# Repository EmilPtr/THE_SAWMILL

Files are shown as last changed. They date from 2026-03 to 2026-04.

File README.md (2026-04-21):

# The Sawmill
The Sawmill is an antweight combat robot I made for the funzies to introduce myself to the wonderful world of combat robotics! This is... THE SAWMILL!!!!!!!!!!!

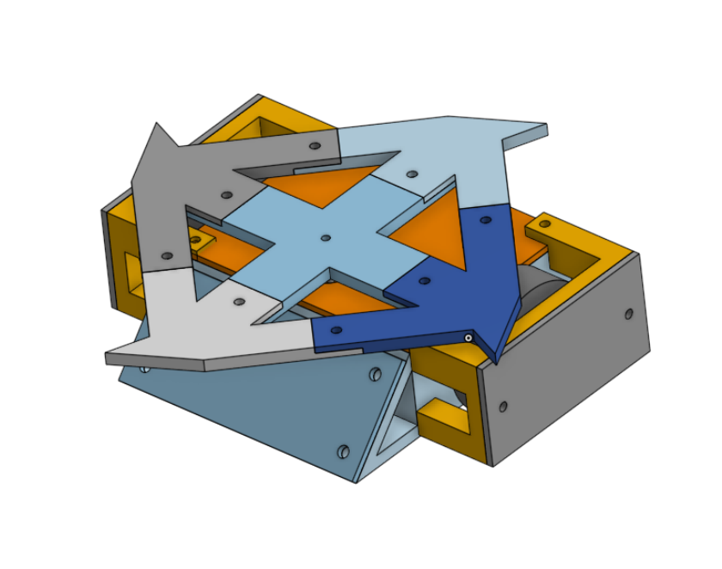
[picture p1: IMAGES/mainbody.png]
mainbody


Inspired by the Fingertech Viper with its horizontal spinner addon, the Sawmill is a wedge x horizontal spinner robot. If the blade decides to combust mid match, it's still a solid wedge bot!

(Disclaimer, this bot is not competetive, and would likely freaking explode in the box, it's made just for fun!)

It is primarily constructed from PLA, with M4 bolts and nuts for joining parts with heat set inserts, and aluminum plates to protect the vulnerable wheels and wedge.

## Design Planning
### Electronics
The electronics are basically your generic RC airplane stack combined with an Arduino Nano to control motors.

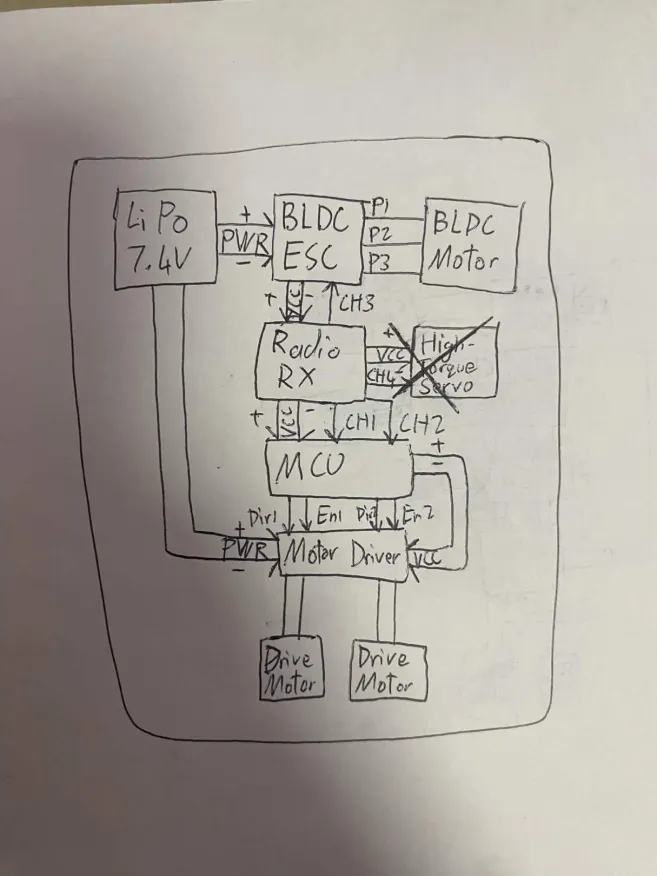
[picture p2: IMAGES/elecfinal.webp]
elec plan


The Arduino nano essentially "hijacks" the signals from the Radio RX, and parses these signals to power a TB6612FNG Motor Driver, the drive motors are N20s geared for 700RPM, while the weapon motor is an A2212 BLDC motor at 2200KV (I know it's a bit fast for a weapon, but :P I no wann spend monny)

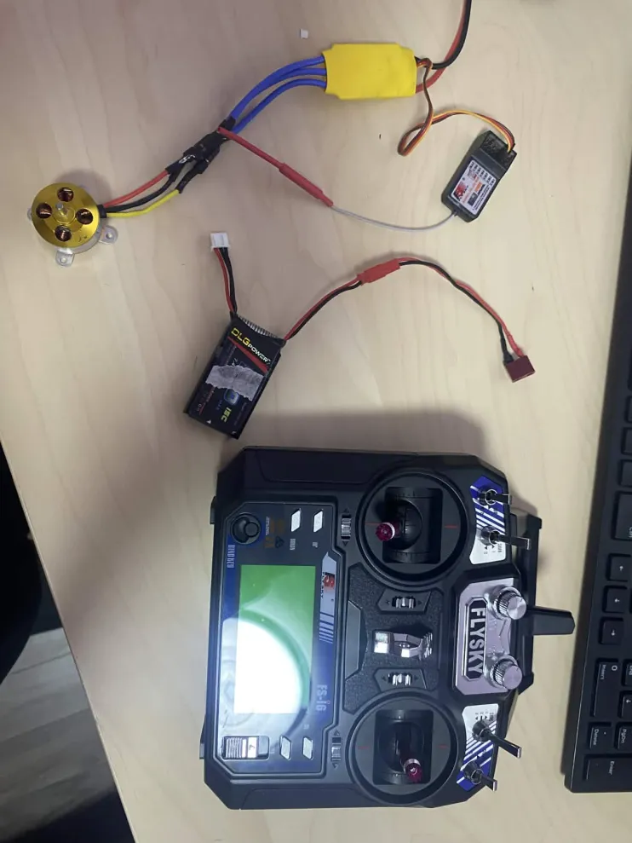
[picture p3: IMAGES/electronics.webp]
physical


Electronics excluding Arduino Nano and N20s, basically your generic RC airplane stack.

### Robot Concept
I am a very indecisive person! It is a very common occurence in my life where the and second/third attempt at something is always the best, while the first is genuinely terrible... I first went for a vertical spinner.

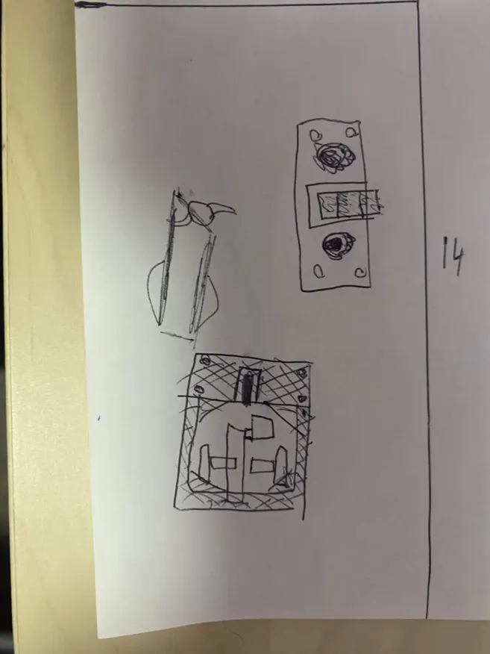
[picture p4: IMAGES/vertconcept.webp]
vert spinner


The vertical spinner concept

After realizing the manufacturing complexity and how accurate my build has to be so the spinner doesnt vibrate itself to death, I decided to switch to a horizontal spinner like Tombstone.

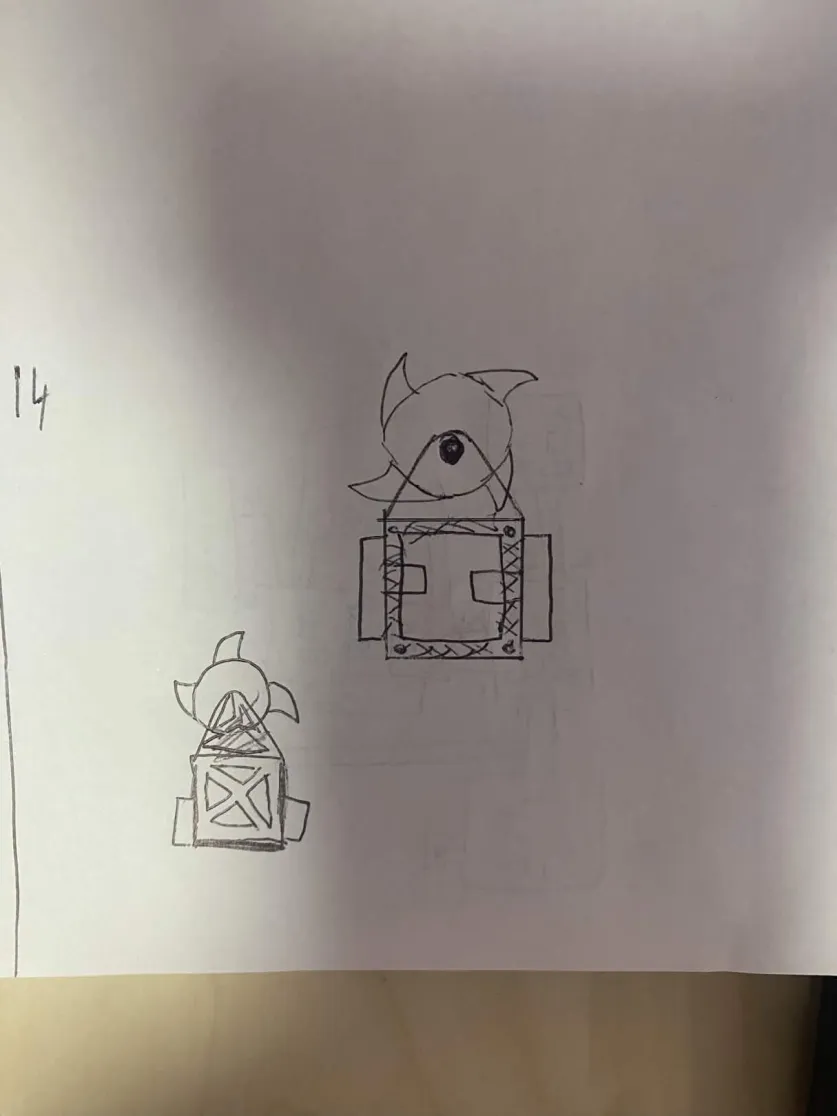
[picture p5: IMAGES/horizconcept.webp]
horizontal spinner


The horizontal spinner concept

I tried this and even got 3 hours of CAD in, I realized it would also be hard to implement, and horizontal spinners like tombstone have the highest self-KO rate, and are NOT beginner friendly

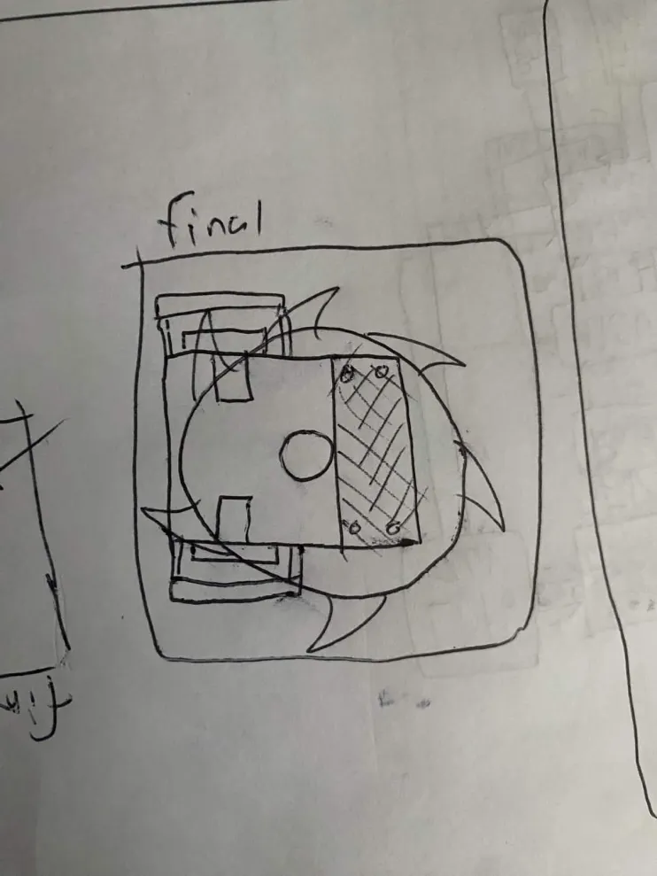
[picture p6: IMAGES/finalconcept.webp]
final


Final concept.

I decided to go with my final design after a few hours of dilly-dallying, and I'm pretty happy with it

## CAD
After I dealt with that kerfuffle... I started the CAD!!! I used OnShape because OnShape is so amazingly BASED and easy to use and FREE! I'm also really familiar with OnShape, but I learned so much from this, especially in Assembly and Drawings!

mainbody

Main body

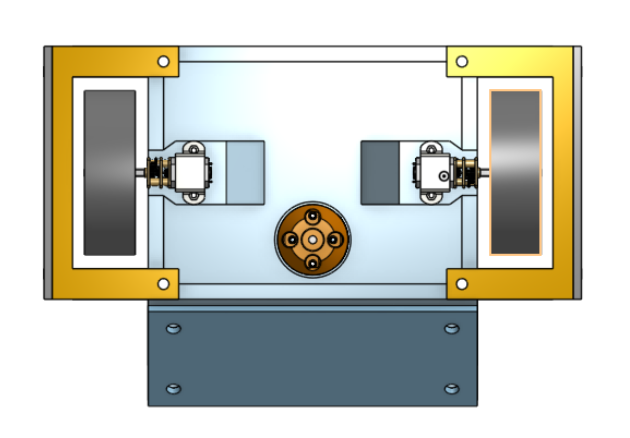
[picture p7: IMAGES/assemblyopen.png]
mainbodyopen


Main body open hood

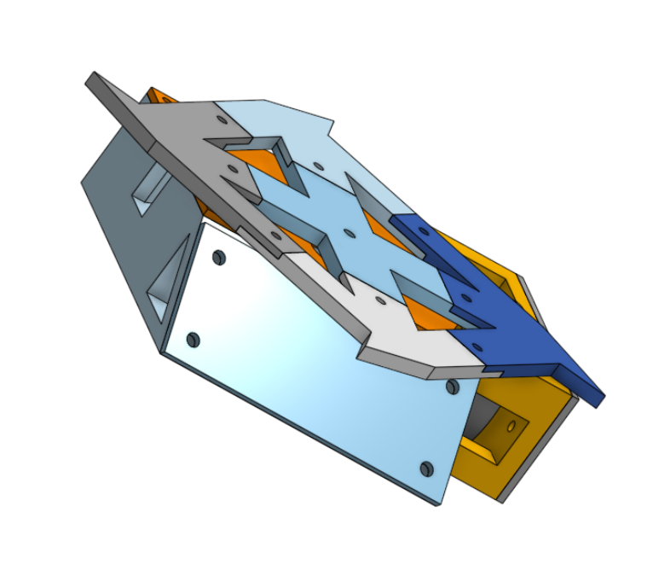
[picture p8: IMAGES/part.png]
part


Part Studio

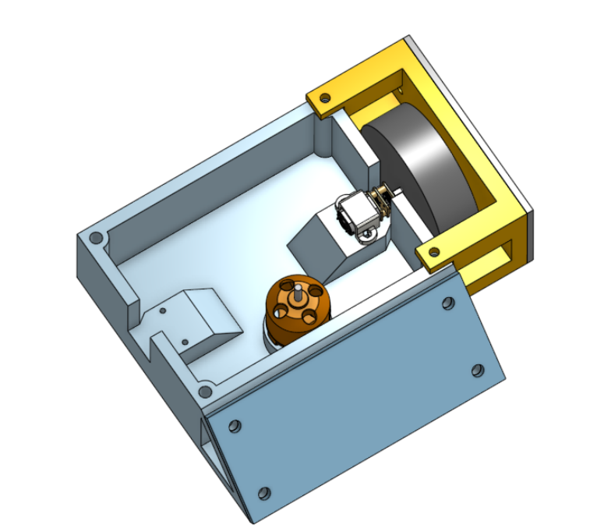
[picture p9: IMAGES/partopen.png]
partopen


Part Studio open hood

### SUPER COOL CAD DRAWING!!!

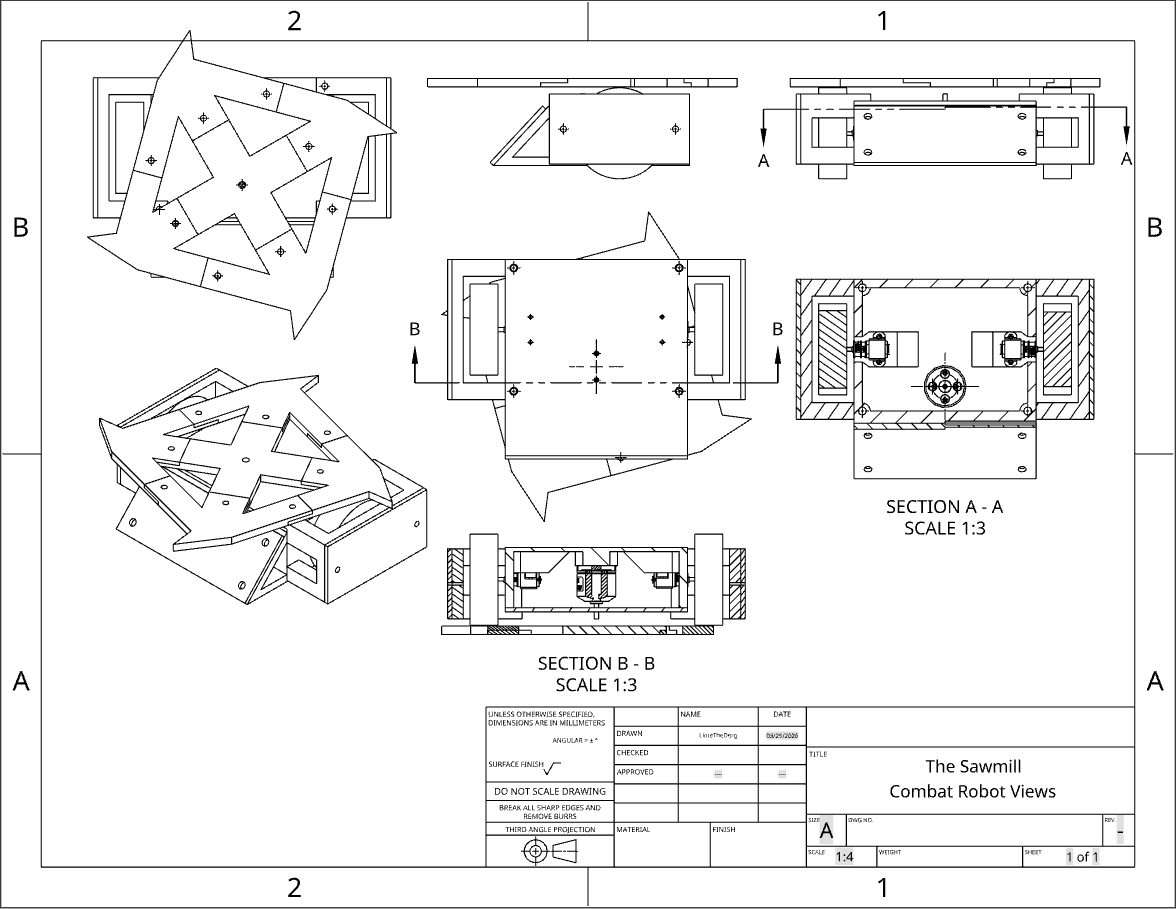
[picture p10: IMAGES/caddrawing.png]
caddrawing


**This was the coolest thing I learned how to do in OnShape!!!*

## Physical build

# Planning
I have assembled majority of the frame and the motors, they are all mounted using machine screws and washers. I have also machined a polycarbonate plate that I forgot to drill a hole in for the weapon shaft. Alongside that, all the electronics are fully complete and the control systems are packed efficiently into the frame. I have yet to assemble the weapon and mount the wheels.

Once I confirm that the chassis is good and can move well, I get to machining the aluminum! I have some plates on hand that I can mark and cut using my FRC team's miter saw and dremel.

Once everything has been put together, it should be fantastic!

## BOM
| Item Name | Amount Needed | Cost to Me (USD) | On Hand |
|---|---|---|---|
| PLA Plastic | ~200g | $0.00 | Yes |
| Aluminum Sheet  | 1 Small Sheet | $11.00 | Yes |
| M4 Hardware | ~10 Sets | $0.00 | Yes |
| M2 Hardware | ~4 Sets | $6.00 | Yes |
| Arduino Nano | 1 | $13.00 | Yes |
| TB6612FNG | 2 | $0.00 | Yes |
| Assorted Wires  | Indeterminate | $0.00 | Yes |
| Wheels | 2 | $0.00 | Yes |
| M3 Hardware | ~2 Sets | $6.00 | Yes |
| 2S LiPo Battery | 1 | $0.00 | Yes |
| N20 DC Motor | 2 | $0.00 | Yes |
| BLDC ESC | 1 | $0.00 | Yes |
| Radio RX | 1 | $0.00 | Yes |
| 2200KV BLDC | 1 | $0.00 | Yes |
| Total | | $36.00 | All rec.|

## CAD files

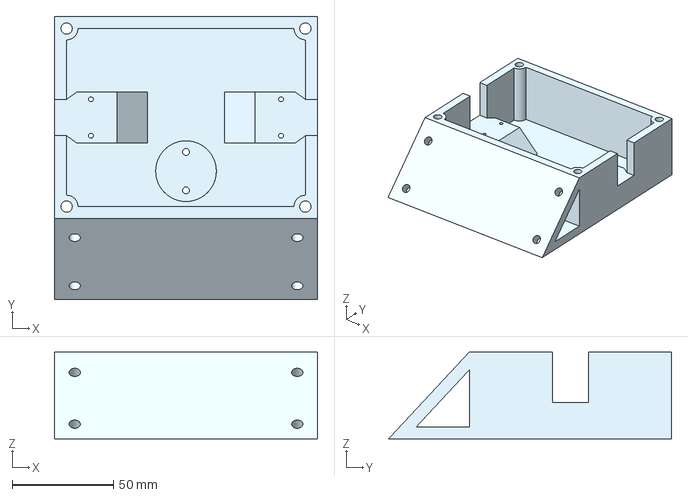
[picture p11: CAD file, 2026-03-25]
3DP_PARTS/Part Studio 1 - Main body.step
130.0 x 140.0 x 43.0 mm

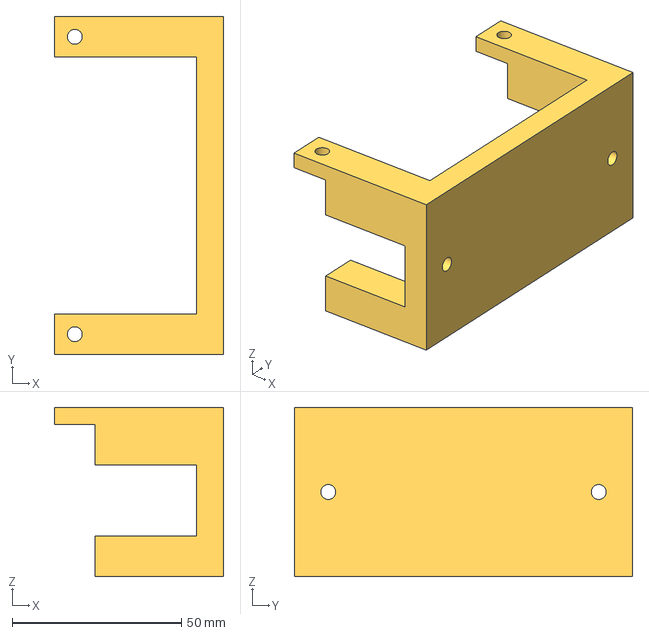
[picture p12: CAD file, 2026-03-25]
3DP_PARTS/Part Studio 1 - Wheel Guard.step
50.0 x 100.0 x 50.0 mm

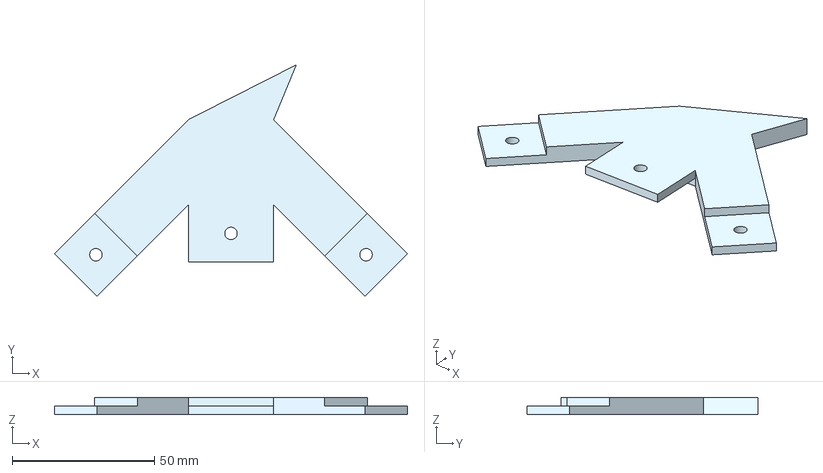
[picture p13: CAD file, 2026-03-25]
3DP_PARTS/Part Studio 1 - Weapon blade DUD.step
124.1 x 81.4 x 6.00 mm

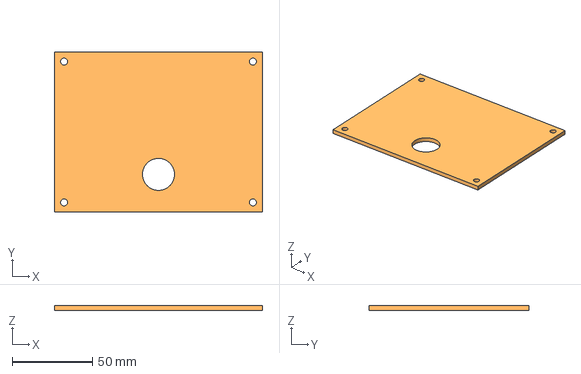
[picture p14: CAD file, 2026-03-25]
3DP_PARTS/Part Studio 1 - Top plate.step
130.0 x 100.0 x 3.00 mm

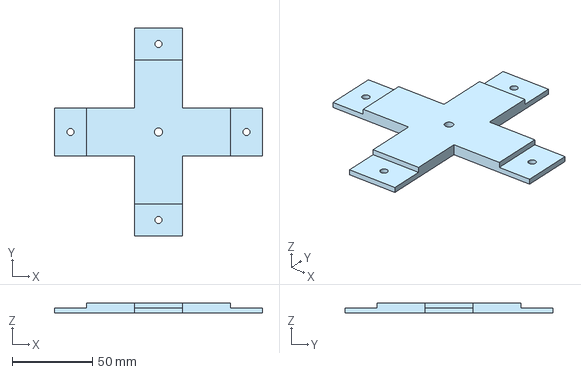
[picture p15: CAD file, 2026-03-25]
3DP_PARTS/Part Studio 1 - Weapon hub.step
130.0 x 130.0 x 6.00 mm

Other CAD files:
3DP_PARTS/Part Studio 1 - Weapon blade UUU.step
3DP_PARTS/Part Studio 1 - Weapon blade UUU (1).step
3DP_PARTS/Part Studio 1 - Weapon blade DUD (1).step

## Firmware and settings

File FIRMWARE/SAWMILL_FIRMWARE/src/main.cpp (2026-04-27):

#include <Arduino.h>

// INPUTS (FS-R6B)
#define TURN_CH1 6   // Receiver CH1
#define FWD_CH2 7    // Receiver CH2

// OUTPUTS (TB6612FNG)
#define R_DIR A1
#define R_PWM 3  
#define L_DIR A4
#define L_PWM 5 

#define OFFSET 1500
#define DEADZONE 55
#define MAX_PULSE 500

void setup() {
  Serial.begin(9600);

  // Set pin modes for inputs
  pinMode(TURN_CH1, INPUT);
  pinMode(FWD_CH2, INPUT);

  // Set pin modes for outputs
  pinMode(R_DIR, OUTPUT);
  pinMode(R_PWM, OUTPUT);
  pinMode(L_DIR, OUTPUT);
  pinMode(L_PWM, OUTPUT);
}

/**
 * Sets motor direction and speed based on input speed value.
 * @param dir_pin The direction control pin for the motor.
 * @param pwm_pin The PWM control pin for the motor.
 * @param speed The desired speed of the motor (-MAX_PULSE to MAX_PULSE).
 */
void setMotor(int dir_pin, int pwm_pin, int speed) {
  if (speed > 0) {
    digitalWrite(dir_pin, HIGH); // Set direction forward
  } else if (speed < 0) {
    digitalWrite(dir_pin, LOW); // Set direction backward
  } else {
    analogWrite(pwm_pin, 0); // Stop motor
    return;
  }

  // Map pulse to motor speed (0 to MAX_PULSE) to (0 to 255)
  int pwm_value = map(abs(speed), 0, MAX_PULSE, 0, 255);
  analogWrite(pwm_pin, pwm_value); // Set motor speed
}

void loop() {
  int fwd_value = pulseIn(FWD_CH2, HIGH, 50000) - OFFSET; // Read forward channel pulse width and apply offset
  int turn_value = pulseIn(TURN_CH1, HIGH, 50000) - OFFSET; // Read turn channel pulse width and apply offset

  // Apply deadzone
  if (abs(fwd_value) < DEADZONE) {
    fwd_value = 0;
  }
  if (abs(turn_value) < DEADZONE) {
    turn_value = 0;
  }

  int left_speed = fwd_value + turn_value; // Calculate left motor speed
  int right_speed = fwd_value - turn_value; // Calculate right motor speed

  setMotor(L_DIR, L_PWM, left_speed);
  setMotor(R_DIR, R_PWM, -right_speed); // Invert right motor

  // Serial output for debugging
  Serial.print("FWD: ");
  Serial.print(fwd_value);
  Serial.print("\tTURN: ");
  Serial.print(turn_value);
  Serial.print("\tLEFT: ");
  Serial.print(left_speed);
  Serial.print("\tRIGHT: ");
  Serial.println(right_speed);

  delay(20); // Small delay for stability
}

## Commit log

2026-03-25 Add all the files
    [Part Studio 1 - Main body.step, Part Studio 1 - Top plate.step, Part Studio 1 - Weapon blade DUD (1).step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]
2026-04-04 Updated BOM
